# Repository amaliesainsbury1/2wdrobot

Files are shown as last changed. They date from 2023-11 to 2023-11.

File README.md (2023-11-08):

# Abrantix Ax2WDRobot

Assembled Ax2WDRobot

## Overview
The Ax2WDRobot is a 2 Wheel-Drive platform based on espressif's ESP32 module. It is WIFI controlled and has the following features:
- WIFI controlled over an integrated Web-Browser. Supports any platform. *No* Android/Iphone app required
- OLED 128x64 display
- 2 independently controlled DC motors
- Omnivision camera module
- Ultrasonic distance sensor
- 6-axis gyroscope (no firmware support so far)
- LiIon powered (18650 cell)
- Charging and programming over USB-C connector
- Easy to assemble; No soldering required

## Assembly
[Assembly instructions](Doc/assembly_instructions.md)

## Programming
[Programming instructions](Doc/programming.md)

## Troubleshooting
*My Ax2WDRobot doesn't turn on*
1. The battery protection circuit prevents powering on as long as there was no initial charge from USB port.
    - Insert the battery, then connect a USB cable (either from PC or from a USB charger) to start charging/enabling the battery.

*I can't update the firmware; Error during firmware Upload*
1. Please make sure that the required drivers are installed on the machine. For manual installation, see https://www.silabs.com/developers/usb-to-uart-bridge-vcp-drivers?tab=downloads
2. The *Ax2WDRobot* requires a charged battery and must be turned on to upload the firmware

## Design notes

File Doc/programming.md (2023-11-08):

# Abrantix Ax2WDRobot Programming

## Overview

The Ax2WDRobot is based on espressif's ESP32. The provided firmware uses arduino-esp32 toolchain for unified Arduino-Style programming.
For firmware development, Visual Studio Code in conjunction with platformio extension are the recommended tools.

## IDE Installation

1. Navigate to https://code.visualstudio.com/download to download and install Visual Studio Code 
   
2. Start Visual Studio Code and open *Extensions*
   
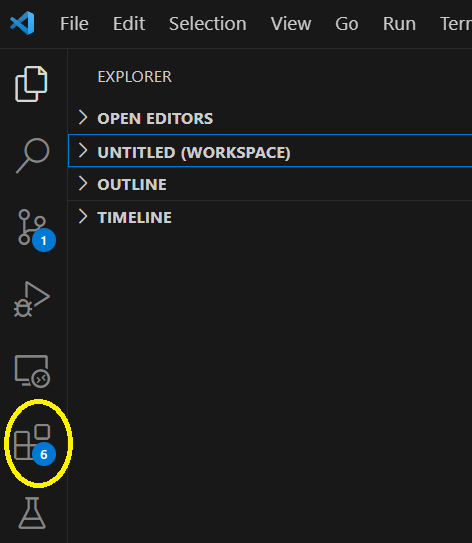
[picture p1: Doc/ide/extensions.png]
Extensions
   

3. In the Extensions screen, search for *platformio* and install it. After installation VS Code has to be restarted.

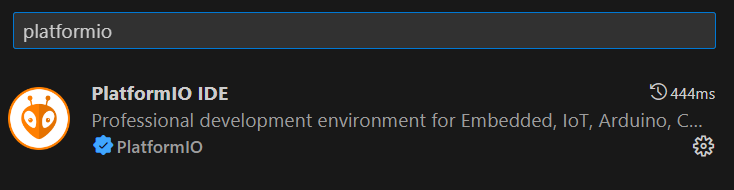
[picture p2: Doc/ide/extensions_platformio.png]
Search Extensions
   

4. Now, you should have a platformio icon in the left toolbar - click on it

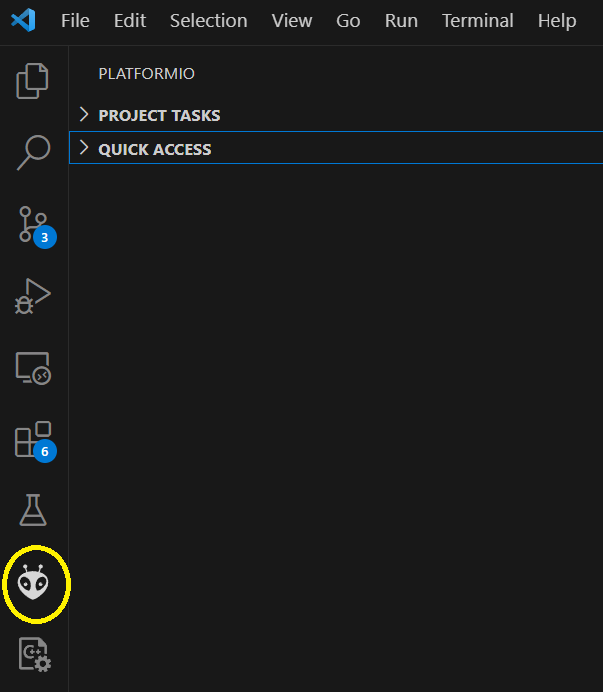
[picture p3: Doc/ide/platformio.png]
Platformio
   

5. In the platformio Home menu, click on *Open project*

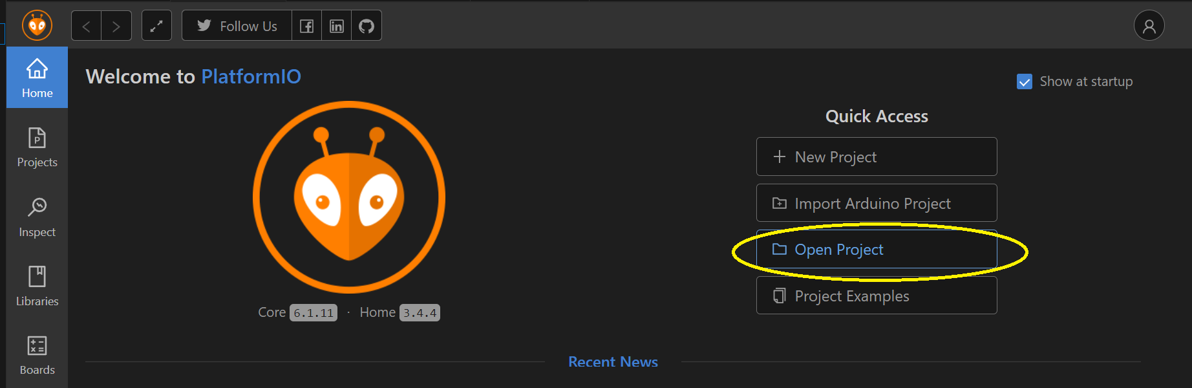
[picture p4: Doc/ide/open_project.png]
Open Project
   

6. Navigate to the folder where you cloned the github project from and open *Ax2WDRobot/firmware/Ax2WDRobot* and click *Open Firmware*.
 
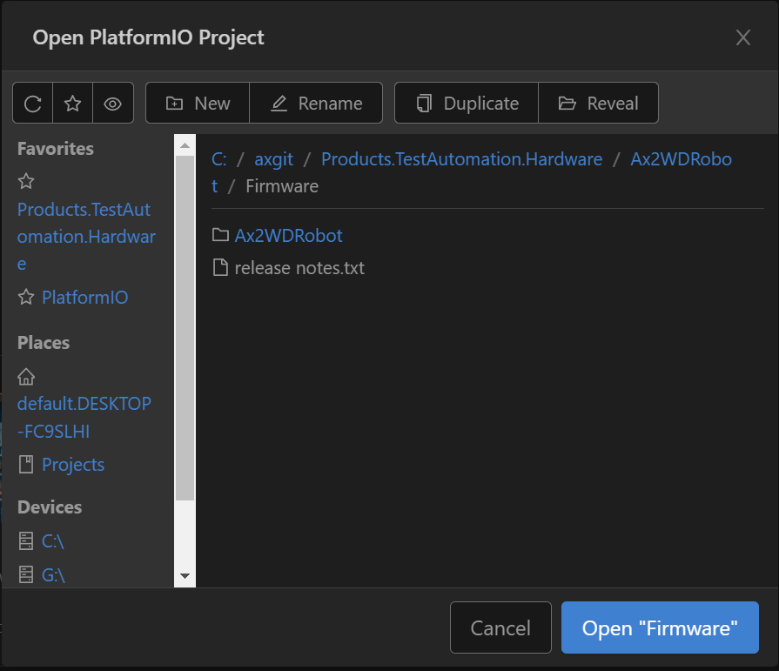
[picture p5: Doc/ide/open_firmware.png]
Open Firmware
   

### Driver installation
The *Ax2WDRobot* uses a Silicon Labs CP210X USB to UART Bridge for communication between PC and robot. Depending on given OS, this driver is already built-in, could be provided as optional Update package or has to be manually installed. In case of a manual installation, please refer to https://www.silabs.com/developers/usb-to-uart-bridge-vcp-drivers?tab=downloads

## Build and upload the firmware
After opening the platformio project, the status bar got some additional icons.
To build, just press the *Check* icon
Build

To upload, first connect the *Ax2WDRobot* to the PC and turn it on. Then, press the *right arrow* icon to build and upload the firmware.
Build

## Build and upload the Filesystem Image
The firmware serves html files from an internal filesystem image which has to be initially loaded, too. This process has to be repeated in case of any change on given files in *data* folder.

1. Click on the platformio icon on the left toolbar
2. Under Project Tasks in the left window, expand *ax2wdrobot->Platform*
3. Execute *Build Filesystem Image*
4. If not already done, connect the *Ax2WDRobot* to the PC and turn it on.
5. Execute *Upload Filesystem Image*

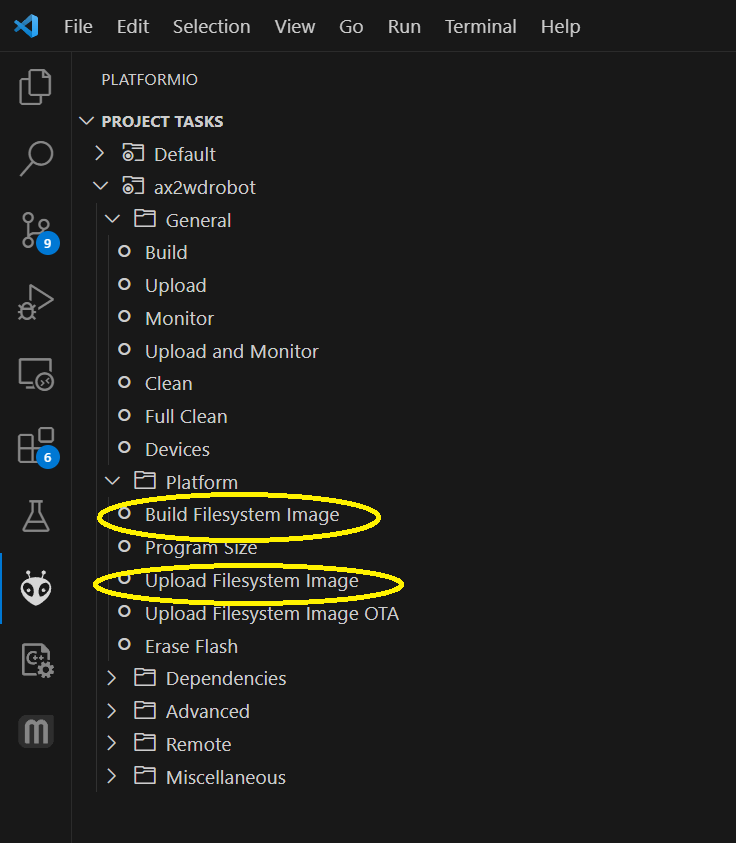
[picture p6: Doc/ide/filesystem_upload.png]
Filesystem upload


For step 4, please ensure that no serial monitor windows are active - otherwise, the filesystem image upload will fail.

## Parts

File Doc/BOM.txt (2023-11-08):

1x Ax2WDRobot Mainboard
1x 18650 Battery i.e. NCR18650B
1x OLED Display 0.96" SSD1306
1x Ultrasonic Sensor RCW-0001
1x Camera-Module OV2640 wide angle 120°
2x TT Gear motor Dual Shaft with Wheel and Dupont wires soldered on
1x Swivel caster roller ~45x28x14mm
1x Zip tie
4x M3 Button Head screw 10mm
2x M3 Button Head screw 14mm
4x M3 Button Head screw 25mm
10x M3 Nut
10x M3 Spring washer
1x roller spacer (3d printed)
2x motor holder (3d printed)

Optional:
1x USB Type A to C data/charging cable

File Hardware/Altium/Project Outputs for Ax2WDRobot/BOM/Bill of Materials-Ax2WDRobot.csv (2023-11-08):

Comment | Description | Designator | Footprint | LibRef | Quantity | LCSCPartNo | Case/Package
1042P | BATTERY HOLDER 18650 SMD TAB | BT1 | FP-1042P-MFG | CMP-19636-000019-1 | 1 | C2988620
22uF/6.3V | Capacitor | C1, C2, C4, C44, C45 | 1608[0603] | Cap | 5 | C59461 | 0603
100nF/50V | Cap Ceramic 0.1uF 50V X7R 20% SMD 0603 125C Paper T/R | C3, C5, C6, C7, C9, C10, C12, C13, C15, C16, C18, C19, C25, C26, C28, C29, C30, C31, C32, C33, C36, C37, C42, C43, C48 | 1608[0603] | C | 25 | C14663 | 0603
15pF/50V | Cap Ceramic 0603 | C8 | 1608[0603] | C | 1 | C1644 | 0603
1uF | CAP CER 1UF 10V X5R 0603 | C11, C14, C17, C20, C22, C23, C34, C38, C40, C41 | 1608[0603] | C | 10 | C15849 | 0603
10uF/10V | Capacitor | C21, C24, C27, C35, C39 | 1608[0603] | C, Cap | 5 | C19702 | 0603
1206 100uF/6.3V | Cap Ceramic 100uF 6.3V X5R ±20% SMD 1206 +85°C Embossed T/R | C49 | FP-CL31-IPC_B | CMP-13271-000821-1 | 1 | C15008
SS34 | 0.5mA@40V 40V Single 3A 0.55V@3A SMA(DO-214AC) Schottky | D1 | DIOM449X264X300L114X135N | EGF1B | 1 | C8678 | SMA
LED-Blue | LED BLUE CLEAR CHIP SMD | D2 | FP-LTST-C193TBKT-5A-MFG | CMP-2000-06624-2 | 1 | C72041 | 0603
LED-Green | LED GREEN CLEAR CHIP SMD | D3 | LED0603G | LED-G | 1 | C72043 | 0603
LED-Red | LED RED CLEAR CHIP SMD | D4 | FP-LTST-C193KRKT-5A-MFG | CMP-2000-06623-2 | 1 | C2286 | 0603
SRV05-4.TCT | RailClamp(R) Low Capacitance TVS Diode Array, 5 pF, 17.5 VC, -55 to 125 degC, 6-Pin SOT23, RoHS, Tape and Reel | D5 | SMTC-SOT23-6_V | CMP-2000-05358-1 | 1 | C85364 | SOT-23-6L
PTC 6V 750mA | PTC RESET FUSE 6V 750MA 1206 | F1 | FP-1206L050YR-MFG | CMP-08606-000073-1 | 1 | C70078 | 1206
22uH/2A | Inductor | L1 | INDM7166X18N | Inductor | 1 | C705336
500mA 1.5K@100MHz | Chip Ferrite Bead, 0603, 1500O @ 100MHz, 0.5O, 25%, 500mA | L2, L3, L4, L5, L6 | 1608[0603] | CMP-0686-00368-3 | 5 | C82155 | 0603
Header 4 female 8.5mm | Header, 4-Pin | P1, P4 | BCS-104-L-S-TE | Header 4 | 2 | C124413
FPC Connector 24 pins, top connect |  | P2 | AFC07-S24ECA-00 | FPC-CONN-24 | 1 | C262643
TYPE-C-31-M-12 | USB Connectors 24 Receptacle 1 8.94*7.3mm RoHS | P3 | HRO_TYPE-C-31-M-12-3D | TYPE-C-31-M-12 | 1 | C165948
Header 2 | Header, 2-Pin | P5, P6 | BCS-102-L-S-TE | Header 2 | 2 | C49661
FS8205 | Dual N-Channel Enhancement Mode Power MOSFET | Q1, Q5 | SOT95P280X145-6N | FS8205 | 2 | C2830320
MMSS8050 | TRANS NPN 25V 1.5A SOT23 | Q2, Q3 | SOT-23 | NPN1 | 2 | C20526 | SOT-23
AO3401A | P-Channel MOSFET, 30 V, 4 A, -55 to 150 degC, 3-Pin SOT-23-3L, RoHS, Tape and Reel | Q4, Q6 | AO-SOT-23-3L_V | CMP-2000-05778-1 | 2 | C15127
27K | Resistor | R1 | J1-0603 | Res3 | 1 | C22967
2K4 | Res General Purpose Thick Film 0603 1% 1/10W ±100ppm/°C Molded SMD Paper T/R | R2 | 1608[0603] | R | 1 | C22940 | 0603
2K7 | Resistor | R3 | J1-0603 | Res3 | 1 | C13167
1k | Res General Purpose Thick Film 0603 1% 1/10W ±100ppm/°C Molded SMD Paper T/R | R4, R6, R9, R14, R27 | 1608[0603] | R | 5 | C21190 | 0603
11K | Resistor | R5 | J1-0603 | Res3 | 1 | C25950 | 0603
1K2 | Resistor | R7 | J1-0603 | Res3 | 1
100R | Resistor | R8 | J1-0603 | Res3 | 1
4k7 | RES SMD 4.7K OHM 1% 1/10W 0603, Res General Purpose Thick Film 0603 1% 1/10W ±100ppm/°C Molded SMD Paper T/R | R10, R11, R15, R16, R20, R25, R26, R31, R32, R33 | 1608[0603] | R | 10 | C23162 | 0603
470R | YAGEO RC0603FR-07470RL SMD Chip Resistor, Thick Film, 470 ohm, 50 V, 0603 [1608 Metric], 100 mW, 1%, RC Series | R17 | 1608[0603] | R | 1 | C23179 | 0603
12k | Res Thick Film 0603 12K Ohm 1% 1/10W 100ppm/C Molded SMD SMD Paper T/R | R18, R19, R21, R22 | 1608[0603] | R | 4 | C22790 | 0603
5k1 | Res Thick Film 0603 5.1KOhm 1% 1/10W 100ppm/C Molded SMD SMD Paper T/R | R23, R24 | 1608[0603] | R | 2 | C23186 | 0603
510R | Res General Purpose Thick Film 0603 1% 1/10W ±100ppm/°C Molded SMD Paper T/R | R28 | 1608[0603] | R | 1 | C23193 | 0603
0R | Res General Purpose Thick Film 0603 1% 1/10W ±100ppm/°C Molded SMD Paper T/R | R29 | 1608[0603] | R | 1 | C21189 | 0603
620R | Res General Purpose Thick Film 0603 1% 1/10W ±100ppm/°C Molded SMD Paper T/R | R30 | 1608[0603] | R | 1 | C23220 | 0603
PCM12SMTR | SWITCH SLIDE SPDT 300MA 6V | SW1 | FP-PCM12SMTR-MFG | CMP-2000-06884-2 | 1 | C109335
B3F-4055 | Tactile Switch, 1 to 50 mA, 100 mOhm Max, 5 to 24 VDC, -25 to 70 degC, 4-Pin THD, RoHS, Bulk | SW2 | OMRON-B3F-4055_AX | CMP-2000-05902-1 | 1 | C84931
MT3608 | High Efficiency 1.2MHz 2A Step Up Converter | U1 | SOT95P280X145-6N | MT3608 | 1 | C84817
TP4056 | Complete single cell Li-Ion battery with a constant current / constant voltage linear charger | U2 | SOP127P600X175-9N | TP4056 | 1 | C16581
TC7SB3157 | 1-of-2 multiplexer/demultiplexer | U3 | SOT-363_MP6D | TC7SB3157CFU | 1 | C2674458
TC118S |  | U4, U5 | SO08 | TC118S | 2 | C88308
CP2102N | Full Speed USB to UART Bridge USB 2.0 3.3V Tube Automotive 28-Pin QFN EP | U6 | QFN28_5X5_SIL | CP2102N-A02-GQFN28 | 1 | C6568 | QFN28
ESP32-WROVER-E | Bluetooth, WiFi 802.11b/g/n, Bluetooth v4.2 + EDR, Class 1, 2 and 3 Transceiver Module 2.4GHz ~ 2.5GHz PCB Trace Surface Mount | U7 | XCVR_ESP32-WROVER | ESP32-WROVER | 1 | C2973667
LM317MDT-TR | 500mA, Medium Current 1.2 to 37 V Adjustable Voltage Regulator, 3-Pin DPAK, Tape and Reel | U8, U9 | TO-252_M | CMP-0244-00074-1 | 2 | C75510 | DPAK
AZ1117EH-3.3V | IC REG LIN 3.3V 800MA SOT223-4 | U10 | SOT-223 | AZ1117EH-3.3V | 1 | C6186 | SOT-223
DW01A | SOT-23-6L Battery Management ICs ROHS | U11 | SOT23-6 | DW01A | 1 | C351410
LIS2DW12TR | ACCEL 2-16G I2C/SPI 12LGA | U12 | FP-LGA12-DM00170568-MFG | CMP-12175-000006-1 | 1 | C189624

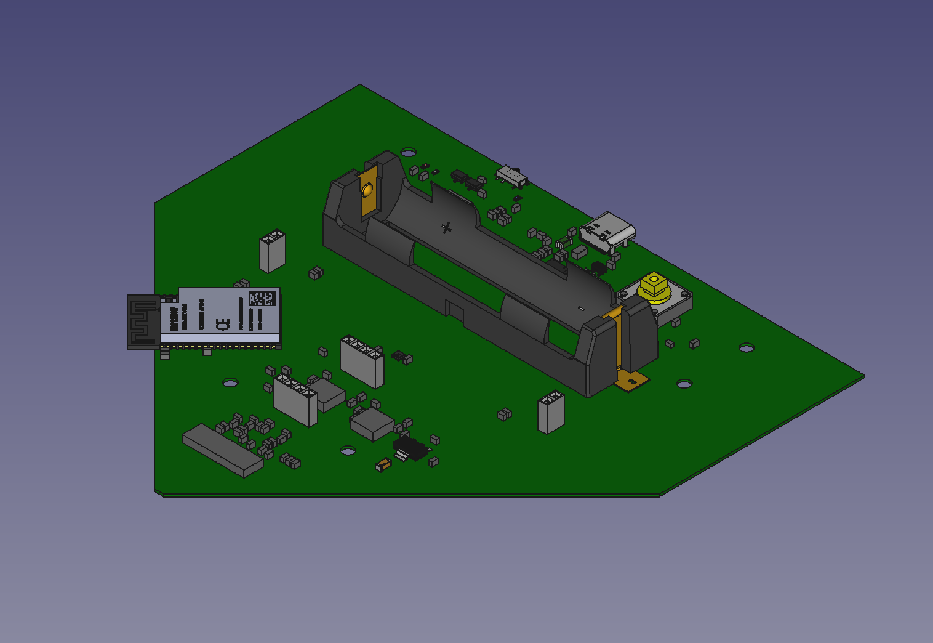
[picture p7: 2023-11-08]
Doc/parts/Mainboard.png

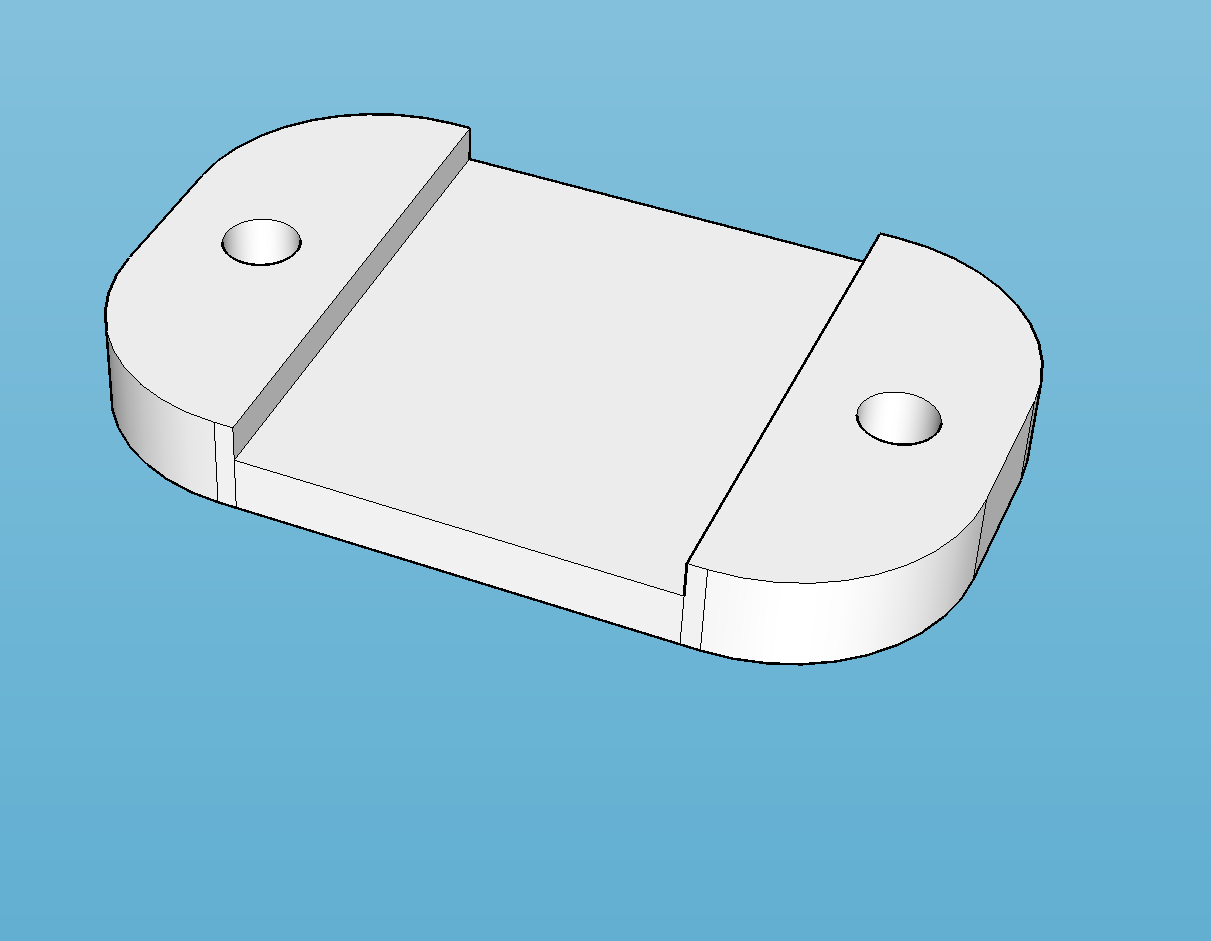
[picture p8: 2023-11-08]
Doc/parts/Roller_spacer.png

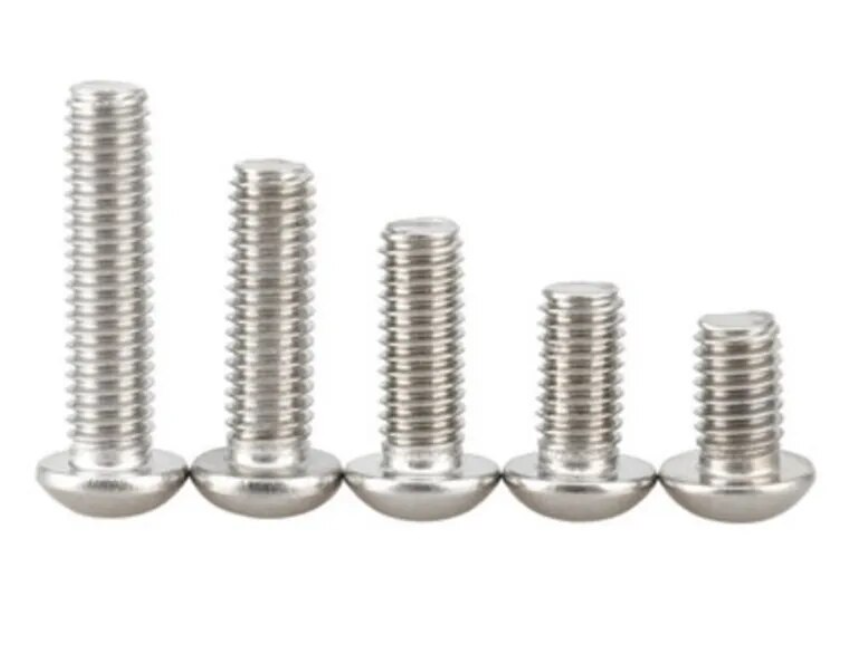
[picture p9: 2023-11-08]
Doc/parts/Screws.png

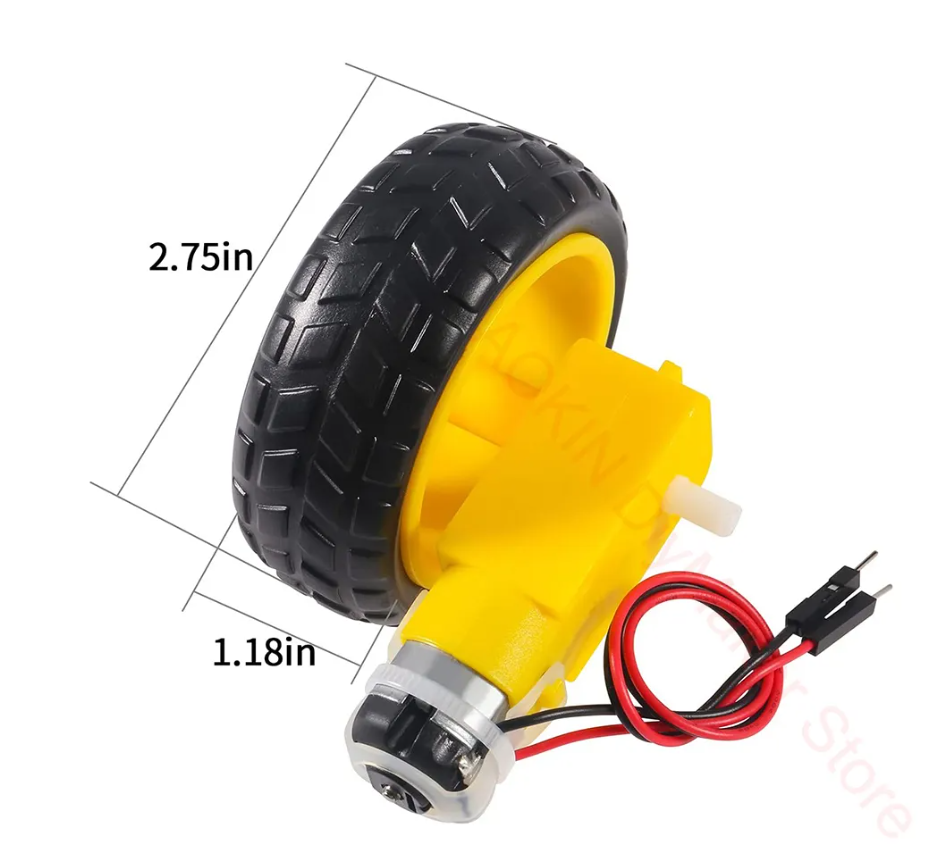
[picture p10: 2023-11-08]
Doc/parts/Motor.png

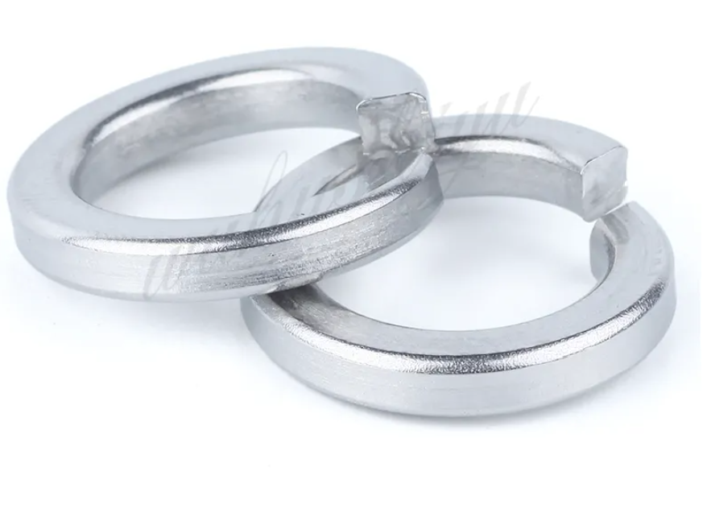
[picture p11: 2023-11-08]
Doc/parts/Washers.png

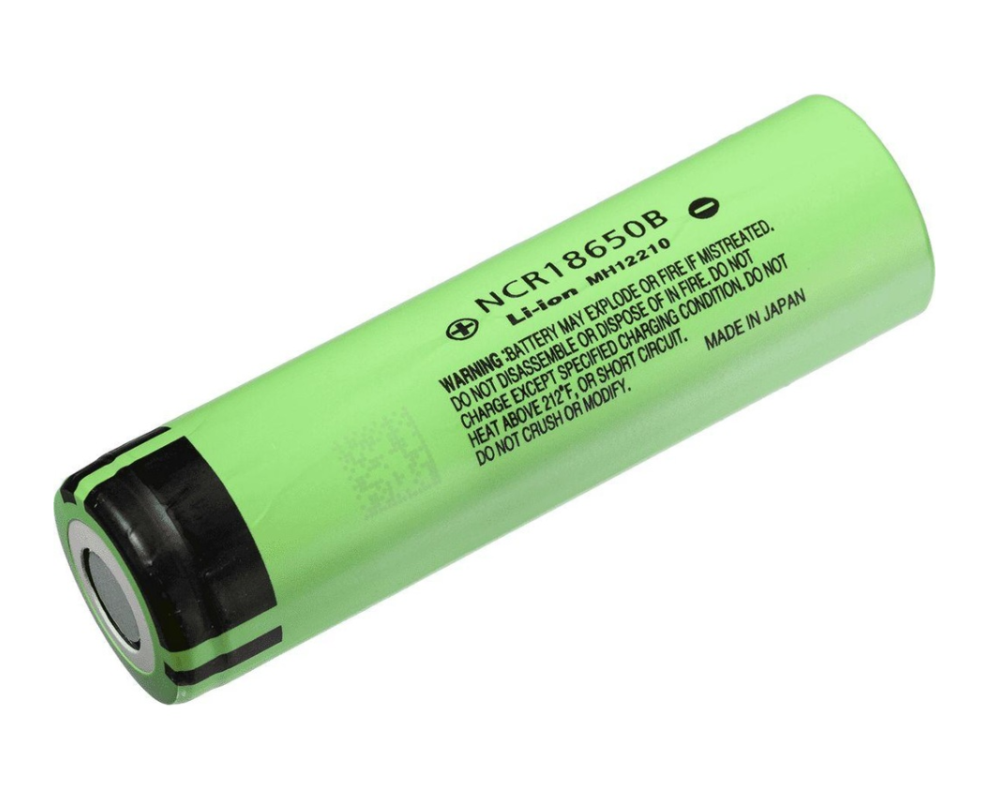
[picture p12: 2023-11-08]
Doc/parts/Battery.png

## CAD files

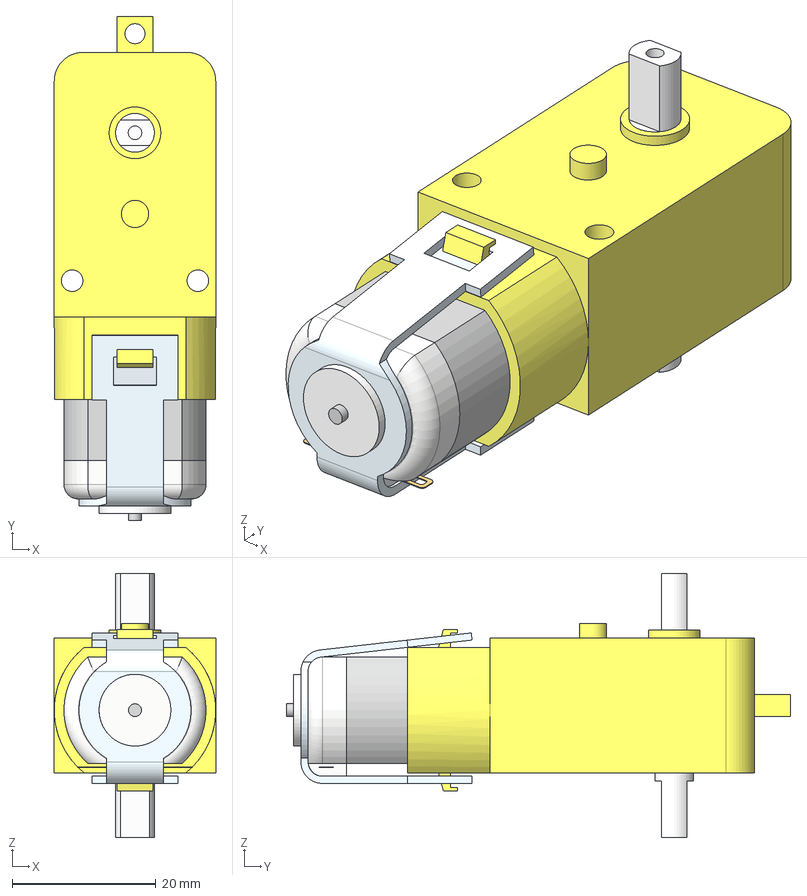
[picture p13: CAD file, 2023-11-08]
Hardware/Altium/TT Motor.step
22.5 x 70.2 x 36.8 mm

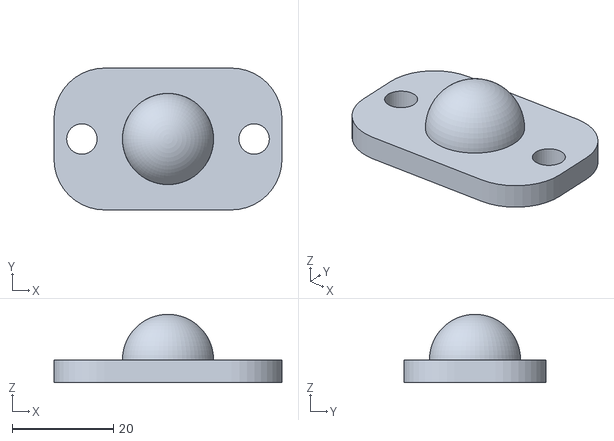
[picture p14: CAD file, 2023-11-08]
Hardware/Housing/roller.stl
45.0 x 28.0 x 13.5

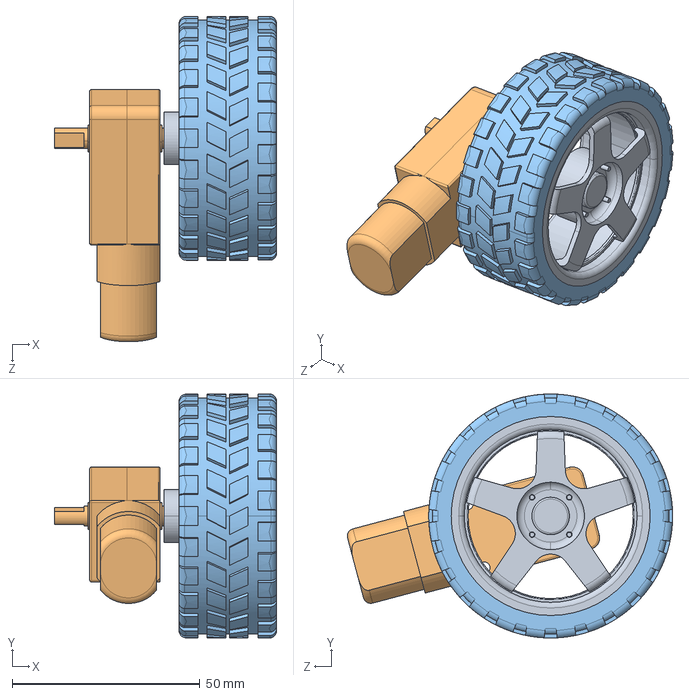
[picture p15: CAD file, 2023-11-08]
Hardware/Altium/dc_motor_and_wheel.STEP
59.2 x 65.0 x 86.7 mm

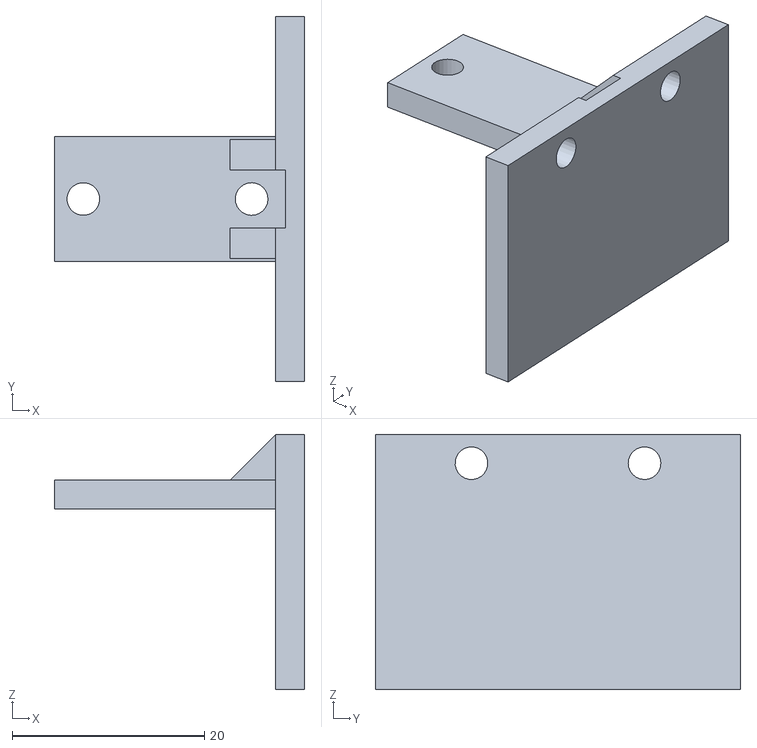
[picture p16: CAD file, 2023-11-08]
Hardware/Housing/motor_holder.stl
26.0 x 38.0 x 26.5

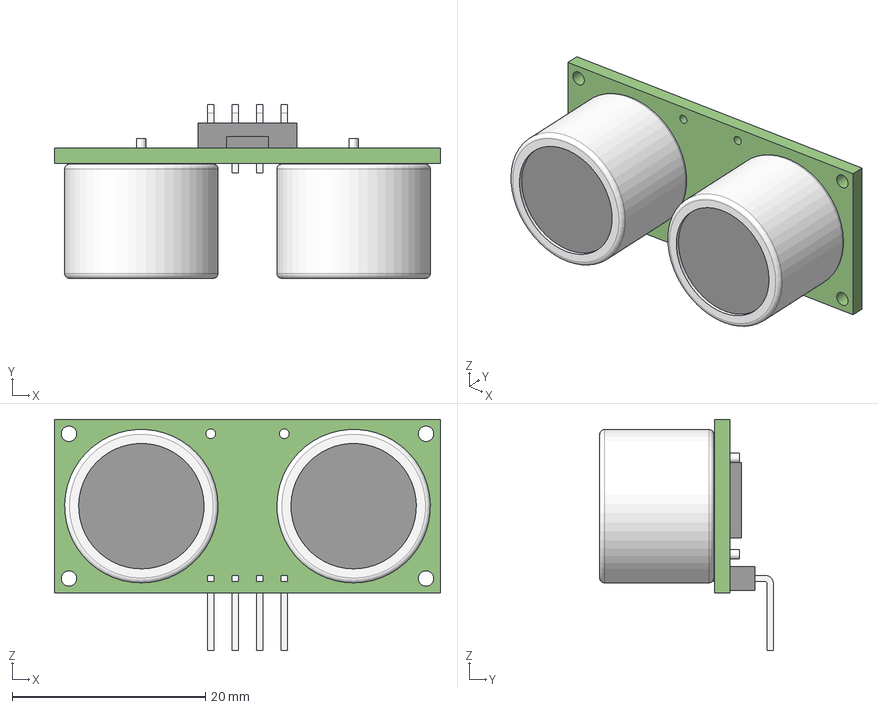
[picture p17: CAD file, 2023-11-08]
Hardware/Altium/RCWL-1601.step
40.0 x 18.0 x 24.0 mm

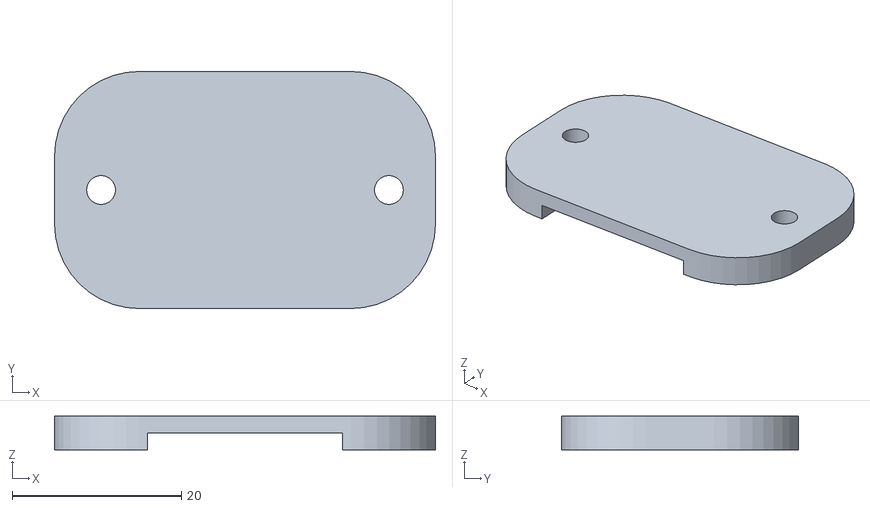
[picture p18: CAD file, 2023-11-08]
Hardware/Housing/roller_spacer.stl
45.0 x 28.0 x 4.00

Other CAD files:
Hardware/Altium/TT_Motor.stl
Hardware/Housing/motor_holder.skp
Hardware/Housing/roller.skp

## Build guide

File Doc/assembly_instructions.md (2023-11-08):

# Abrantix Ax2WDRobot Assembly instructions

## Parts

- 1x Ax2WDRobot Mainboard
- 1x 18650 Battery i.e. NCR18650B
- 1x OLED Display 0.96" SSD1306
- 1x Ultrasonic Sensor RCW-0001
- 1x Camera-Module OV2640 wide angle 120°
- 2x TT Gear motor Dual Shaft with Wheel and Dupont wires soldered on
- 1x Swivel caster roller ~45x28x14mm
- 1x Zip tie
- 4x M3 Button Head screw 10mm
- 2x M3 Button Head screw 14mm
- 4x M3 Button Head screw 25mm
- 10x M3 Nut
- 10x M3 Spring washer
- 1x roller spacer (3d printed)
- 2x motor holder (3d printed)

Optional:
- 1x USB Type A to C data/charging cable

## Assembly Step 1

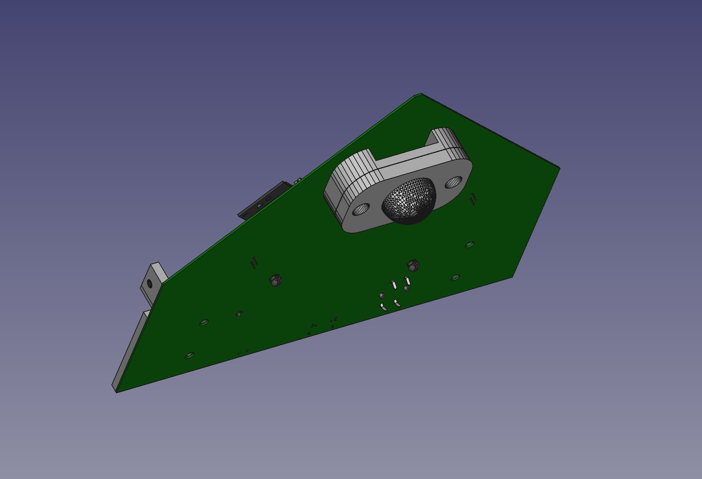
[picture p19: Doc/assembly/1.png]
Step 1


### Required parts
- 1x Ax2WDRobot Mainboard
- 1x Swivel caster roller
- 1x roller spacer (3d printed)
- 2x M3 Button Head screw 14mm
- 2x M3 Nut
- 2x M3 Spring washer

### Instructions
Grab the Ax2WDRobot Mainboard and screw on the swivel caster roller and roller spacer to the bottom of the Mainboard by using two M3x14mm screws

## Assembly Step 2

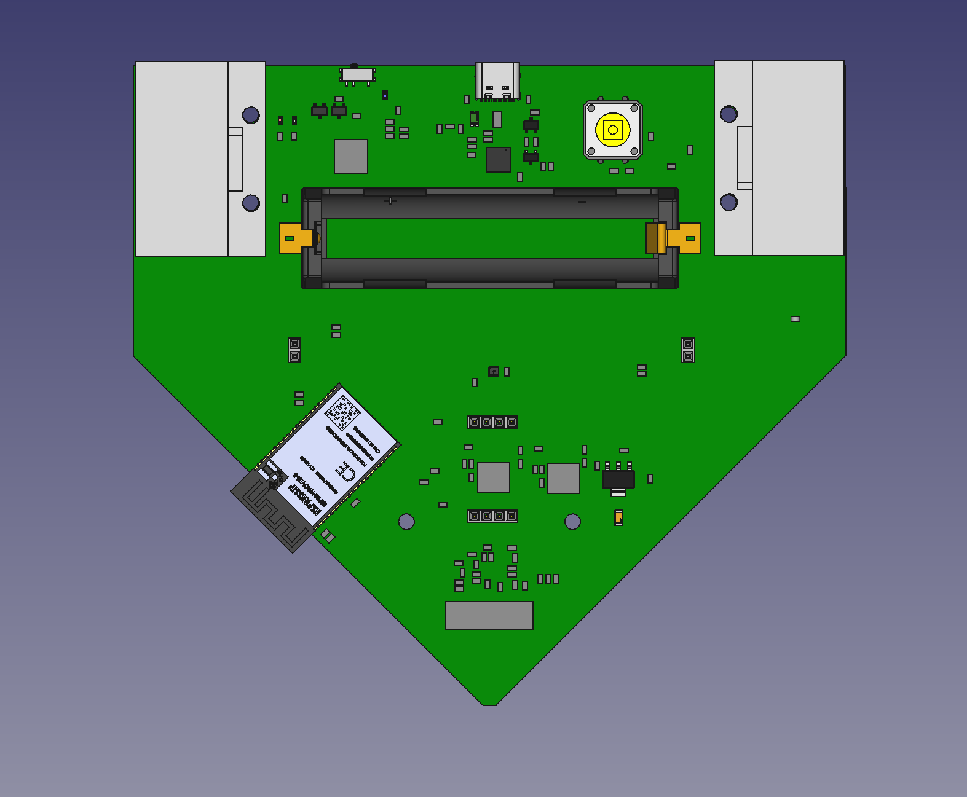
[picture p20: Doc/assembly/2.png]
Step 2


### Required parts
- 2x motor holder (3d printed)
- 4x M3 Button Head screw 10mm
- 4x M3 Nut
- 4x M3 Spring washer

### Instructions
Screw on the two motor holders by using M3x10mm screws

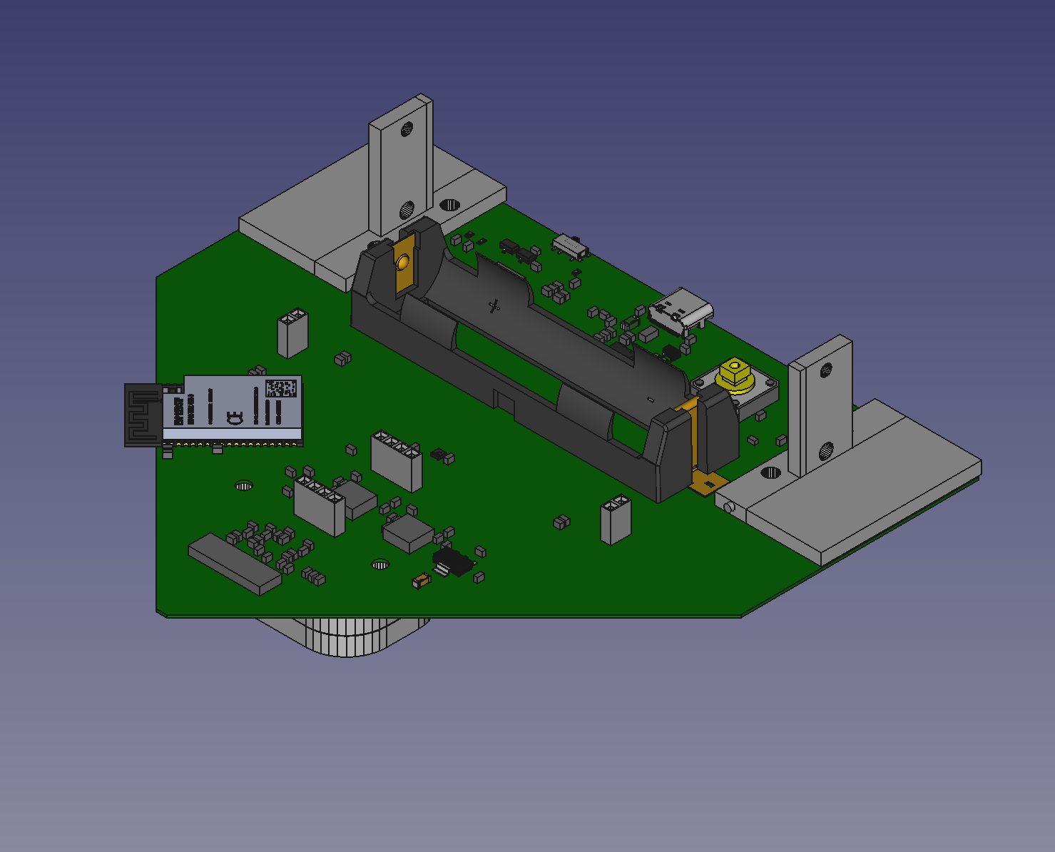
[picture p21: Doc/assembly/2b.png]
Result Step 2


## Assembly Step 3

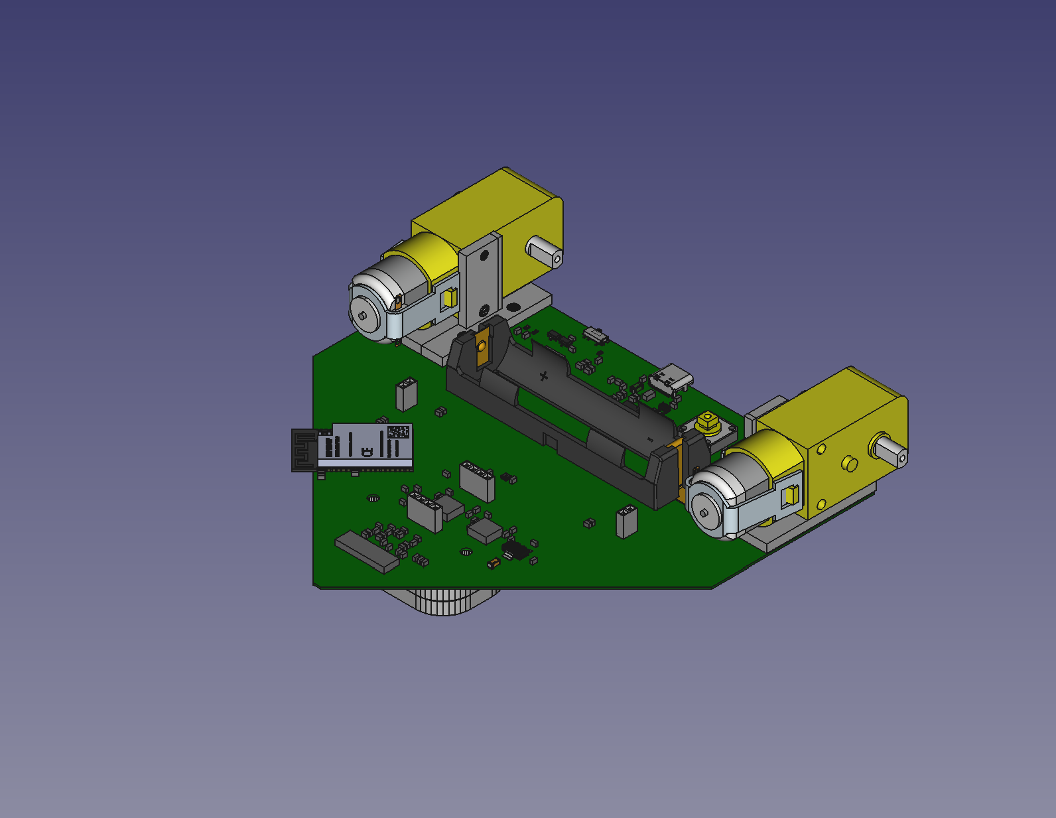
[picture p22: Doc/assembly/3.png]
Step 3


### Required parts
- 2x TT Gear motor assembly
- 4x M3 Button Head screw 25mmm
- 4x M3 Nut
- 4x M3 Spring washer

### Instructions
Screw on the two motors to the holders by using M3x25mm screws

## Assembly Step 4

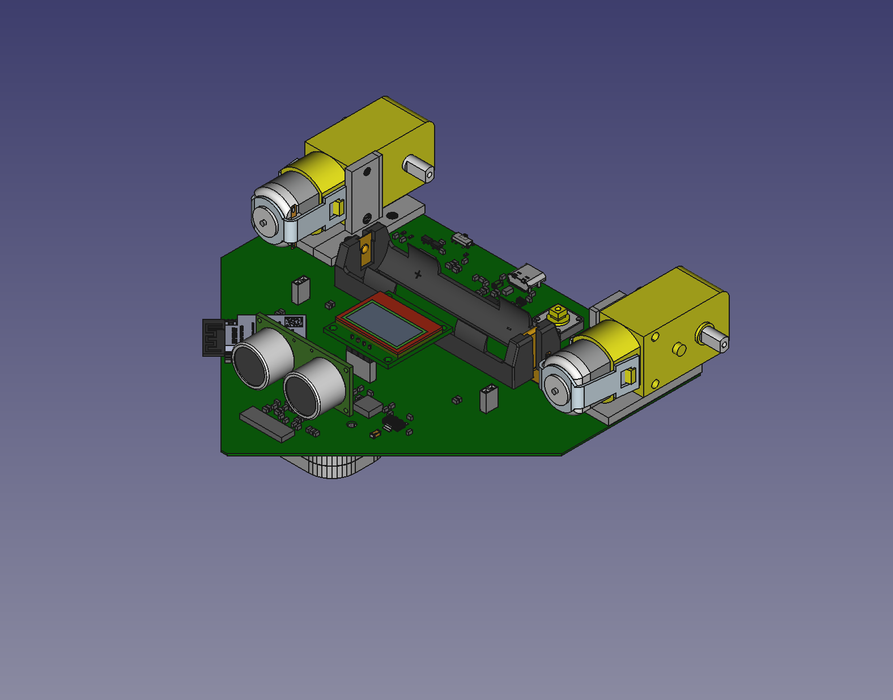
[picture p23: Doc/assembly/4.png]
Step 4


### Required parts
- 1x Camera-Module OV2640 wide angle 120°
- 1x OLED Display 0.96" SSD1306
- 1x Ultrasonic Sensor RCW-0001

### Instructions
Unlock the cam connector by sliding the grey locking clip to the front edge of the mainboard. 
Insert the Camera-Module into the connector by facing its contacts upside
Lock the cam connector by sliding the grey locking clip back
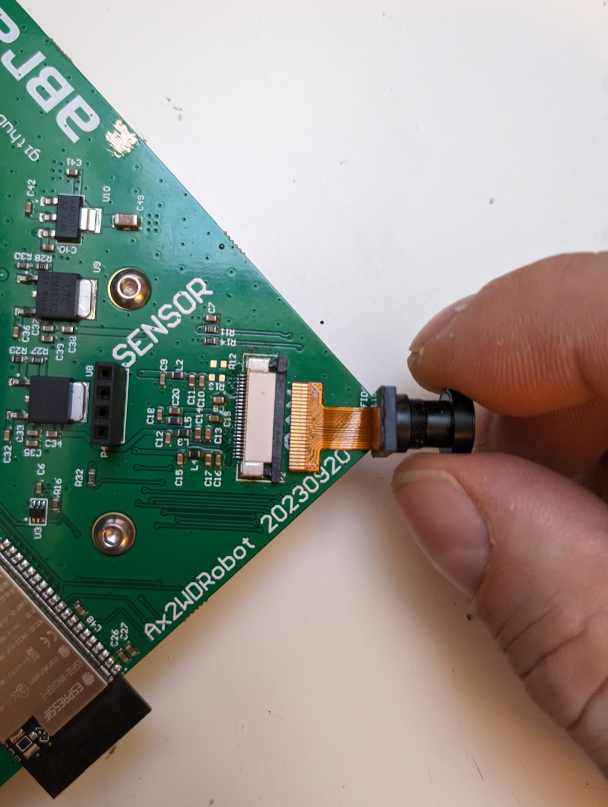
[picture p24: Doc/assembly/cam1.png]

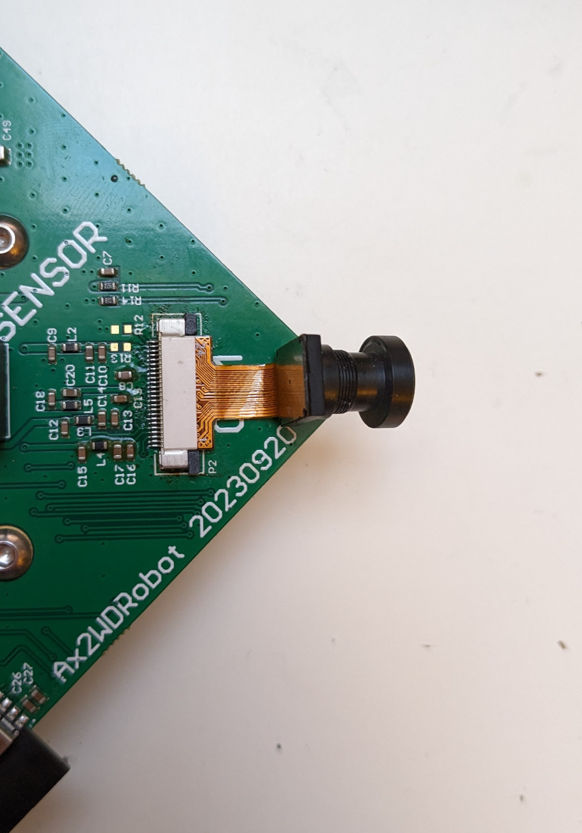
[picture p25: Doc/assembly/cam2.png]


Slightly bend the pins of the Ultrasonic distance sensor by ~30° and insert it into the *SENSOR* connector
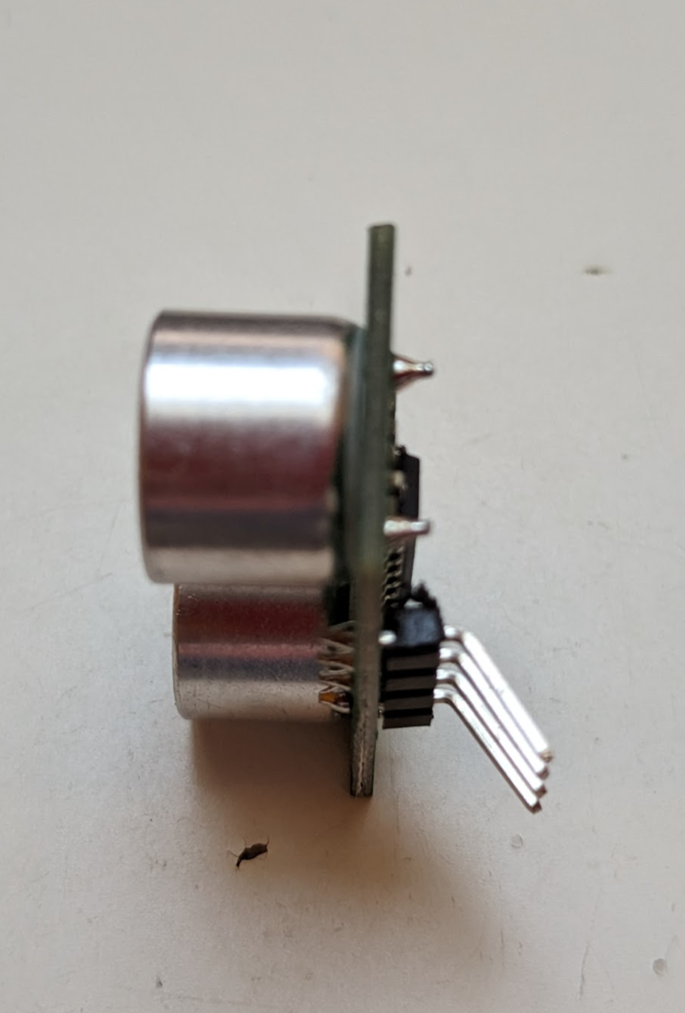
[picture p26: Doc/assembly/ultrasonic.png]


Insert the OLED Display into the *DISPLAY* connector

Plug in the motor connectors (red means *+*, black means *-*). Please connect them "cross-over": the left motor goes to the connector on the right side of the mainboard and vice-versa. Add a zip tie to the cables for better fixation

Finally, insert the 18650 battery into the battery compartment. **IMPORTANT: Check polarity of battery before inserting.**

## Glueing
For better fixation, it's recommended to apply a small amount of (hot) glue to the motor Dupont connectors and the cam.

Final

Now, your Ax2WDRobot is ready to be charged and flashed.

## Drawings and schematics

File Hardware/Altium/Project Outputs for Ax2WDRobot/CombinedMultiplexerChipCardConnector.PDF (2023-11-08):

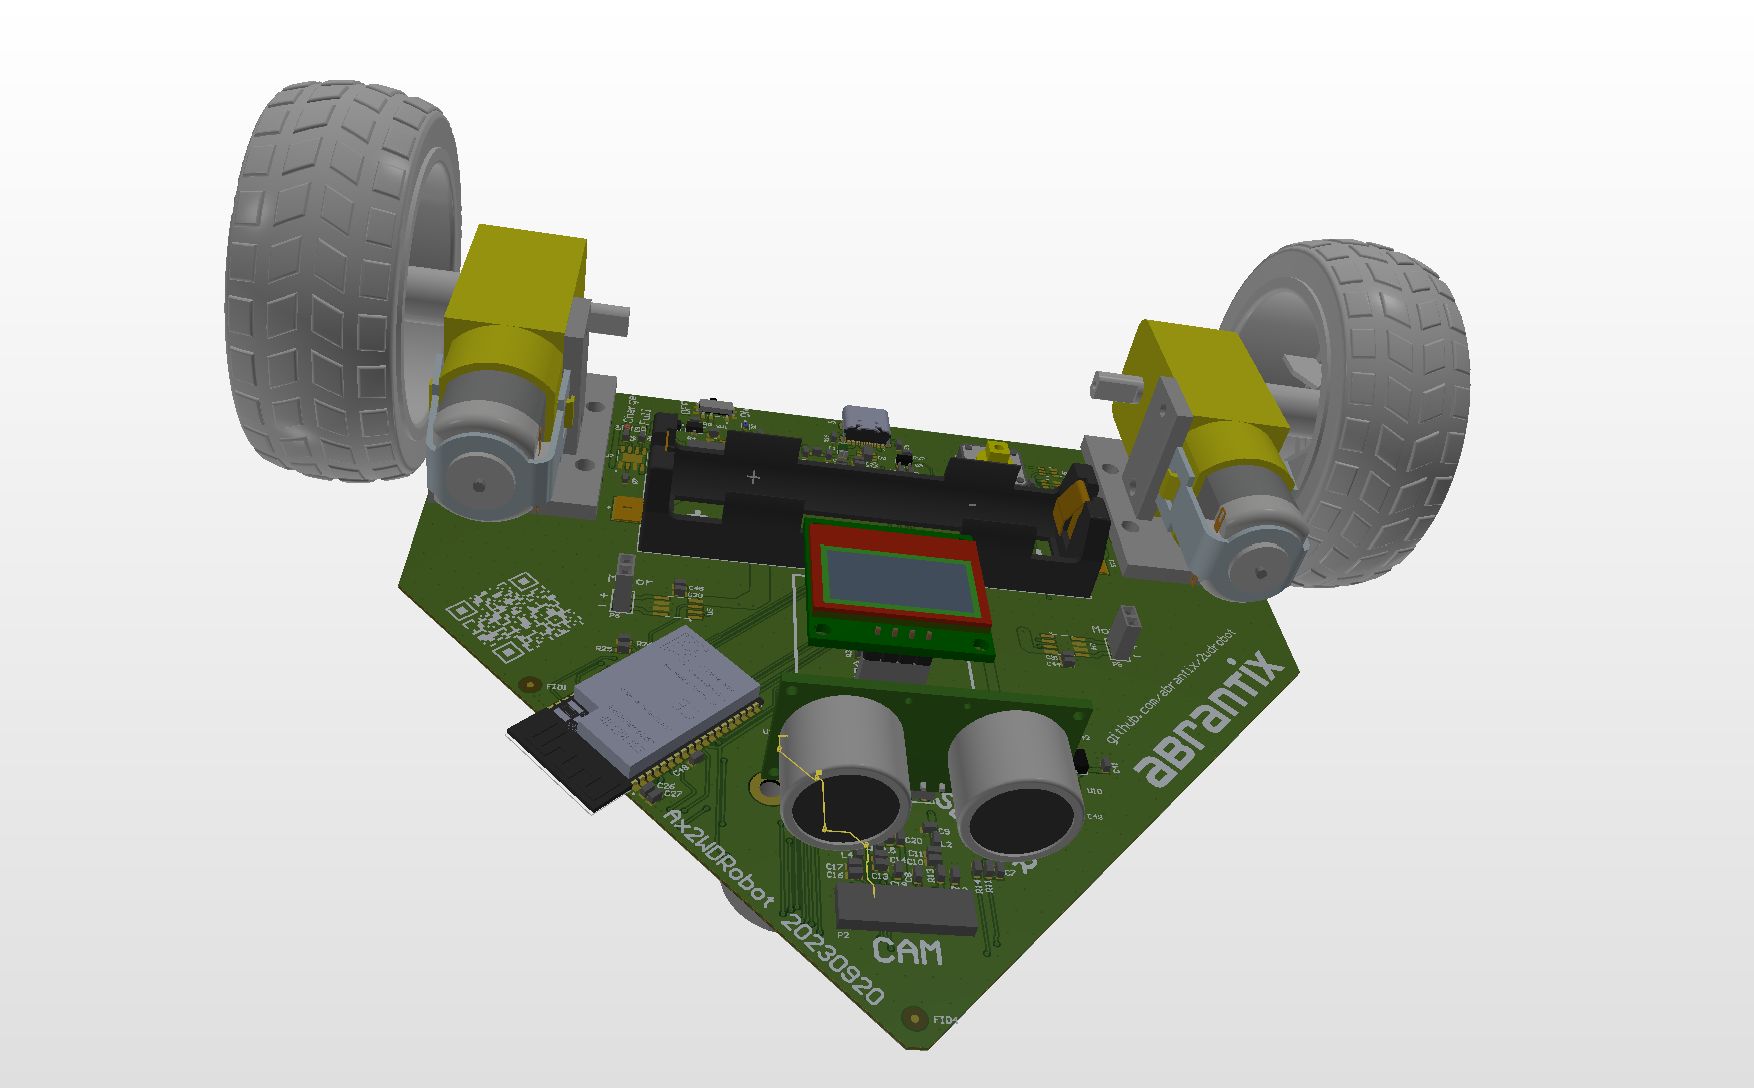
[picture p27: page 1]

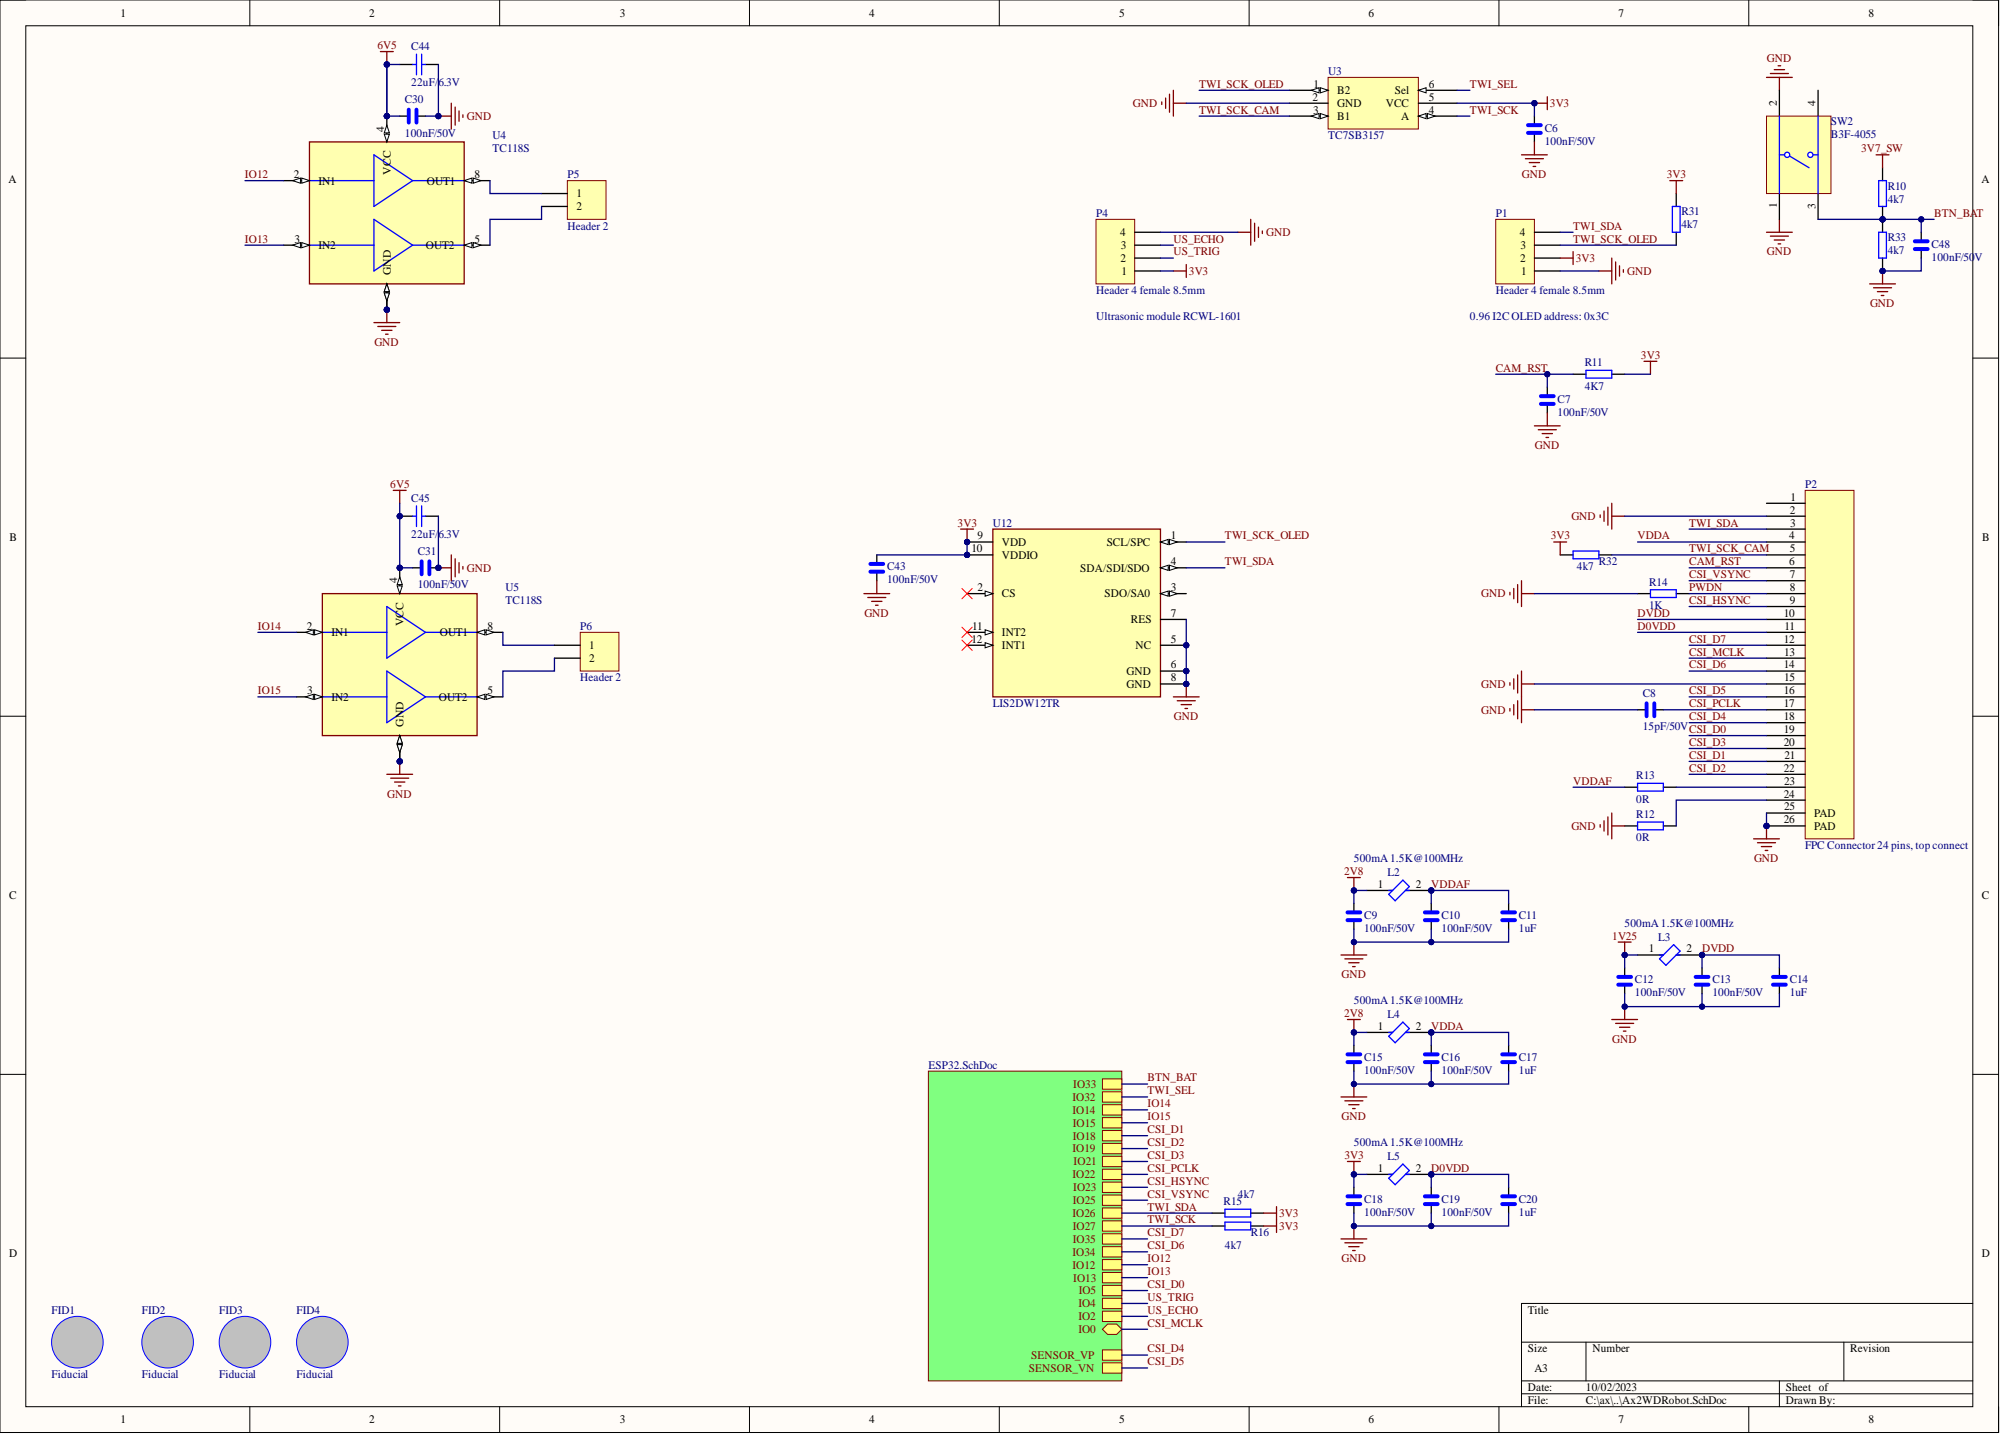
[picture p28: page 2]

FPC Connector 24 pins, top connect

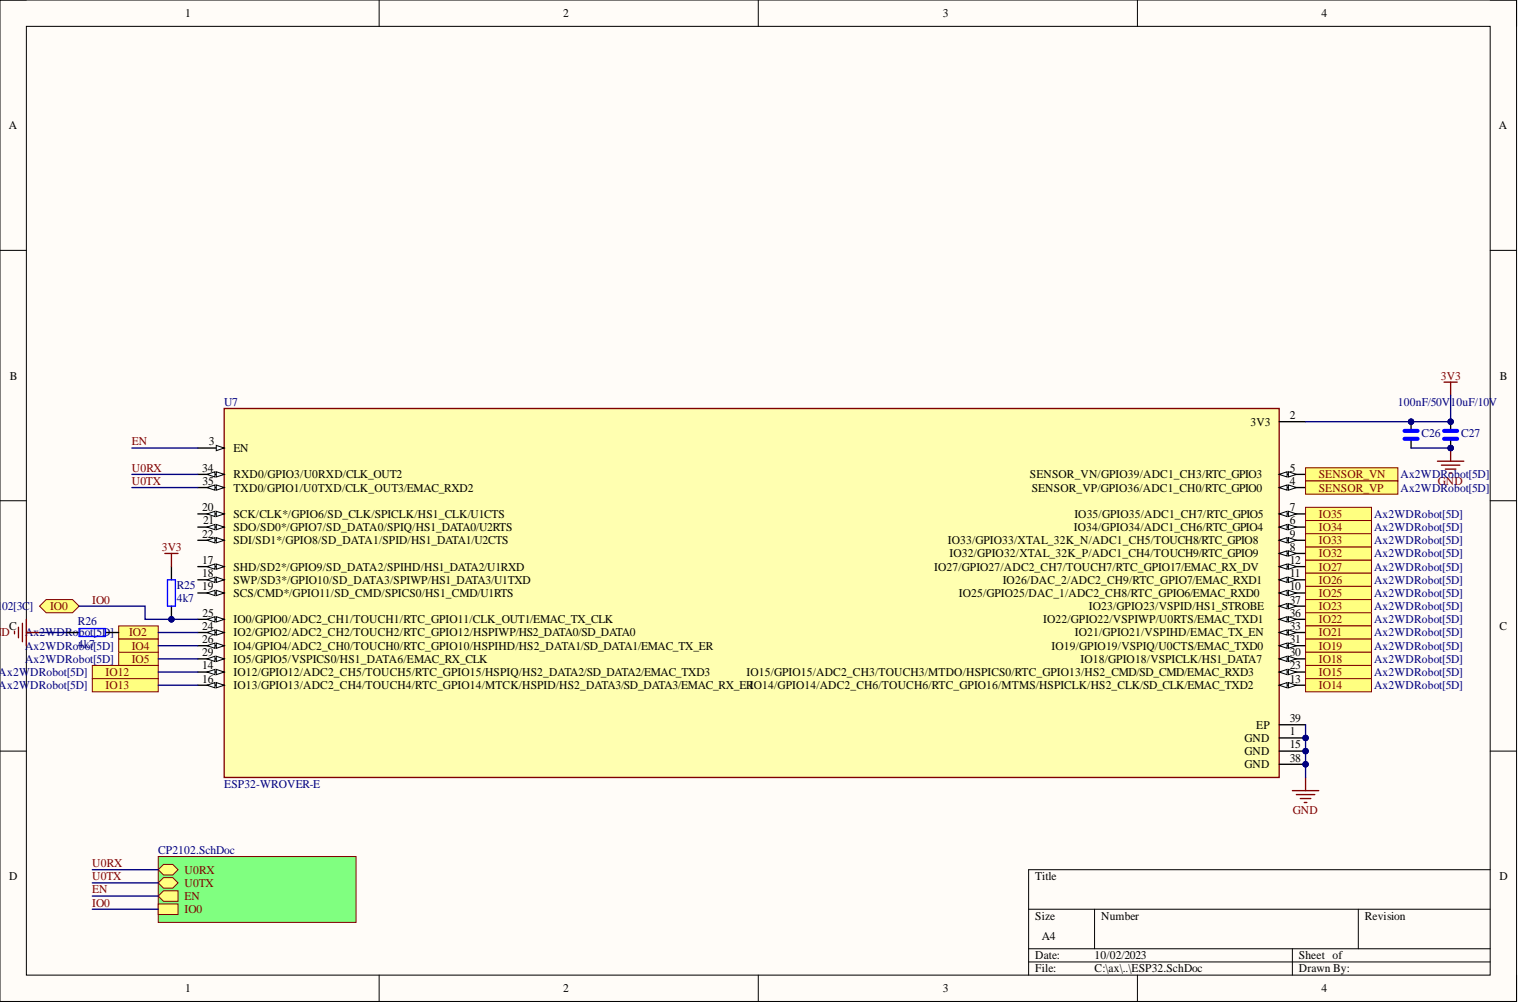
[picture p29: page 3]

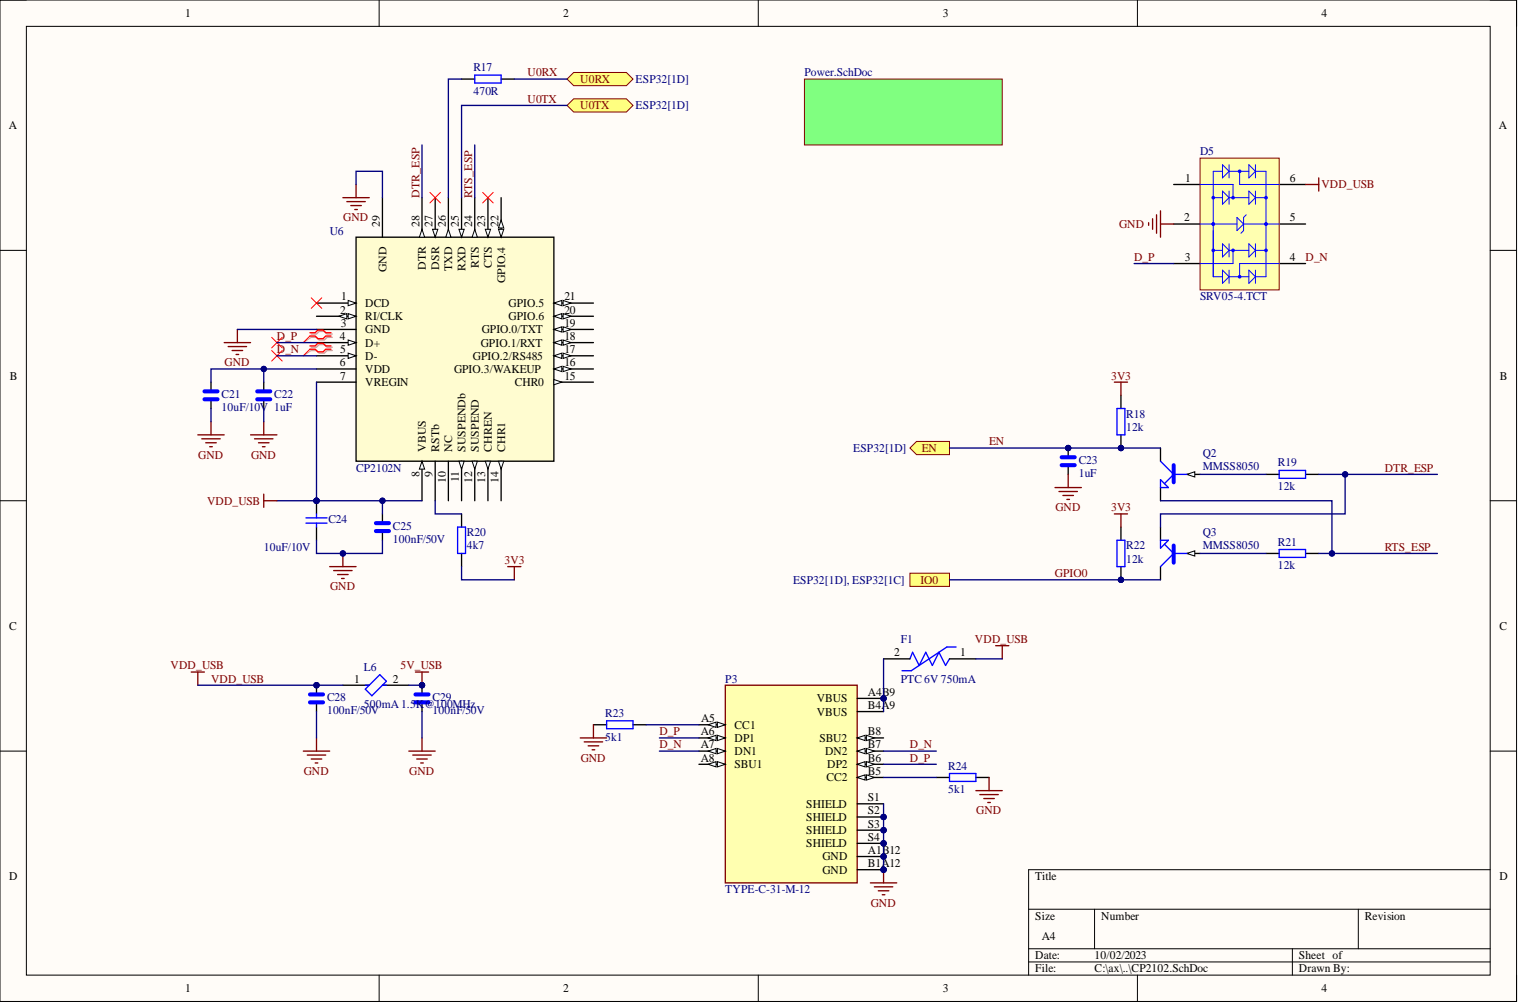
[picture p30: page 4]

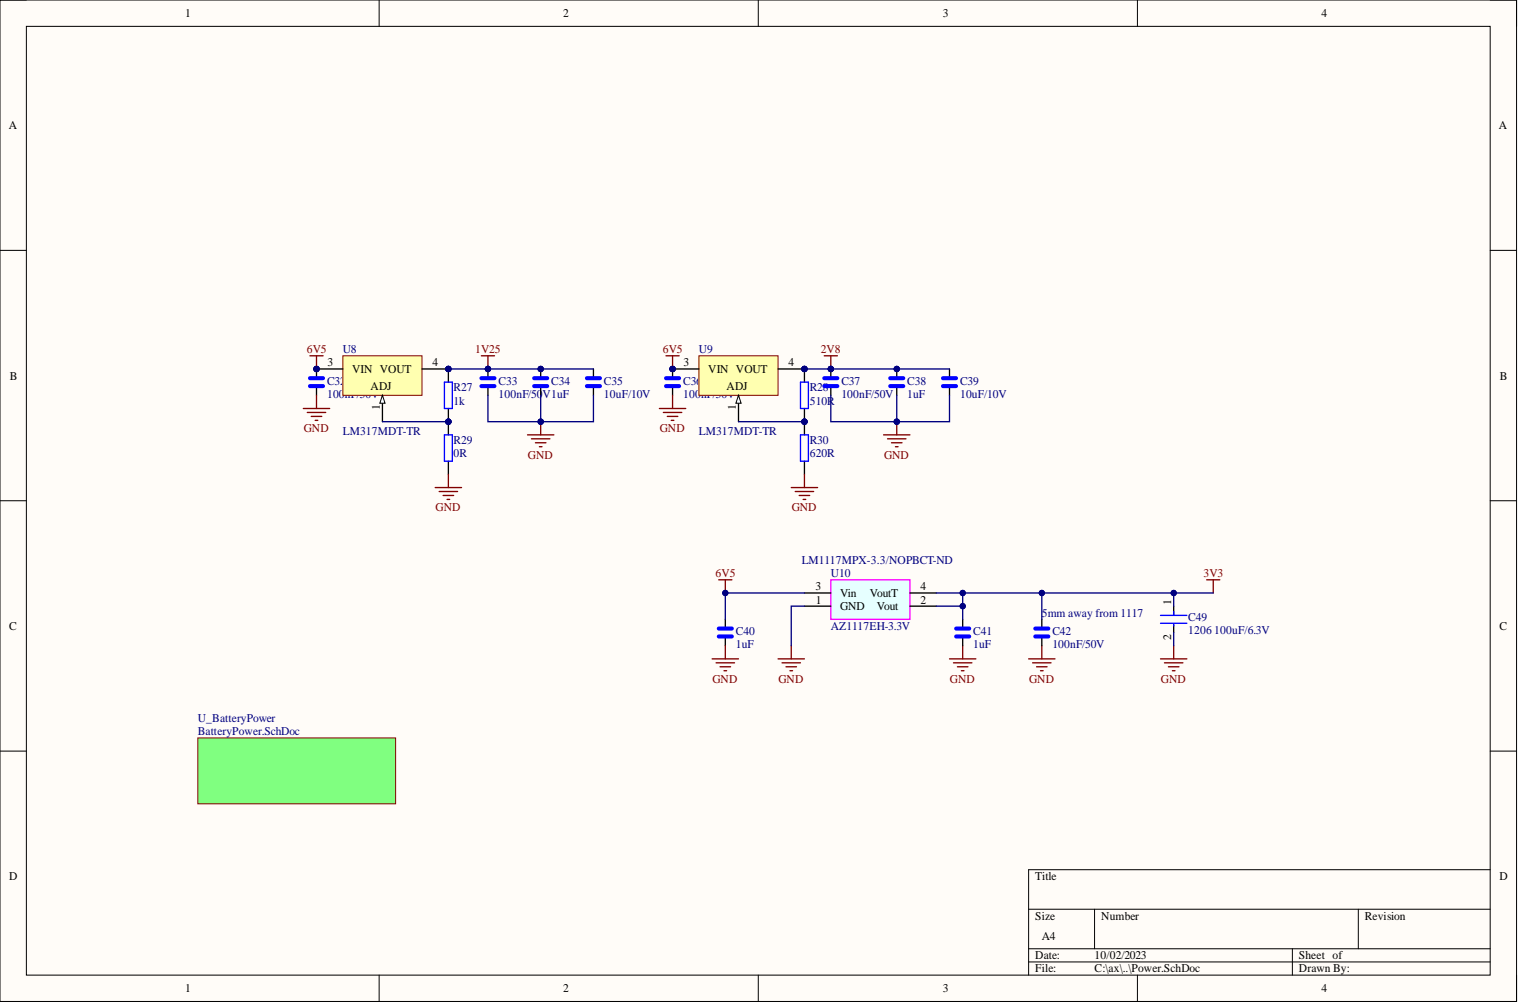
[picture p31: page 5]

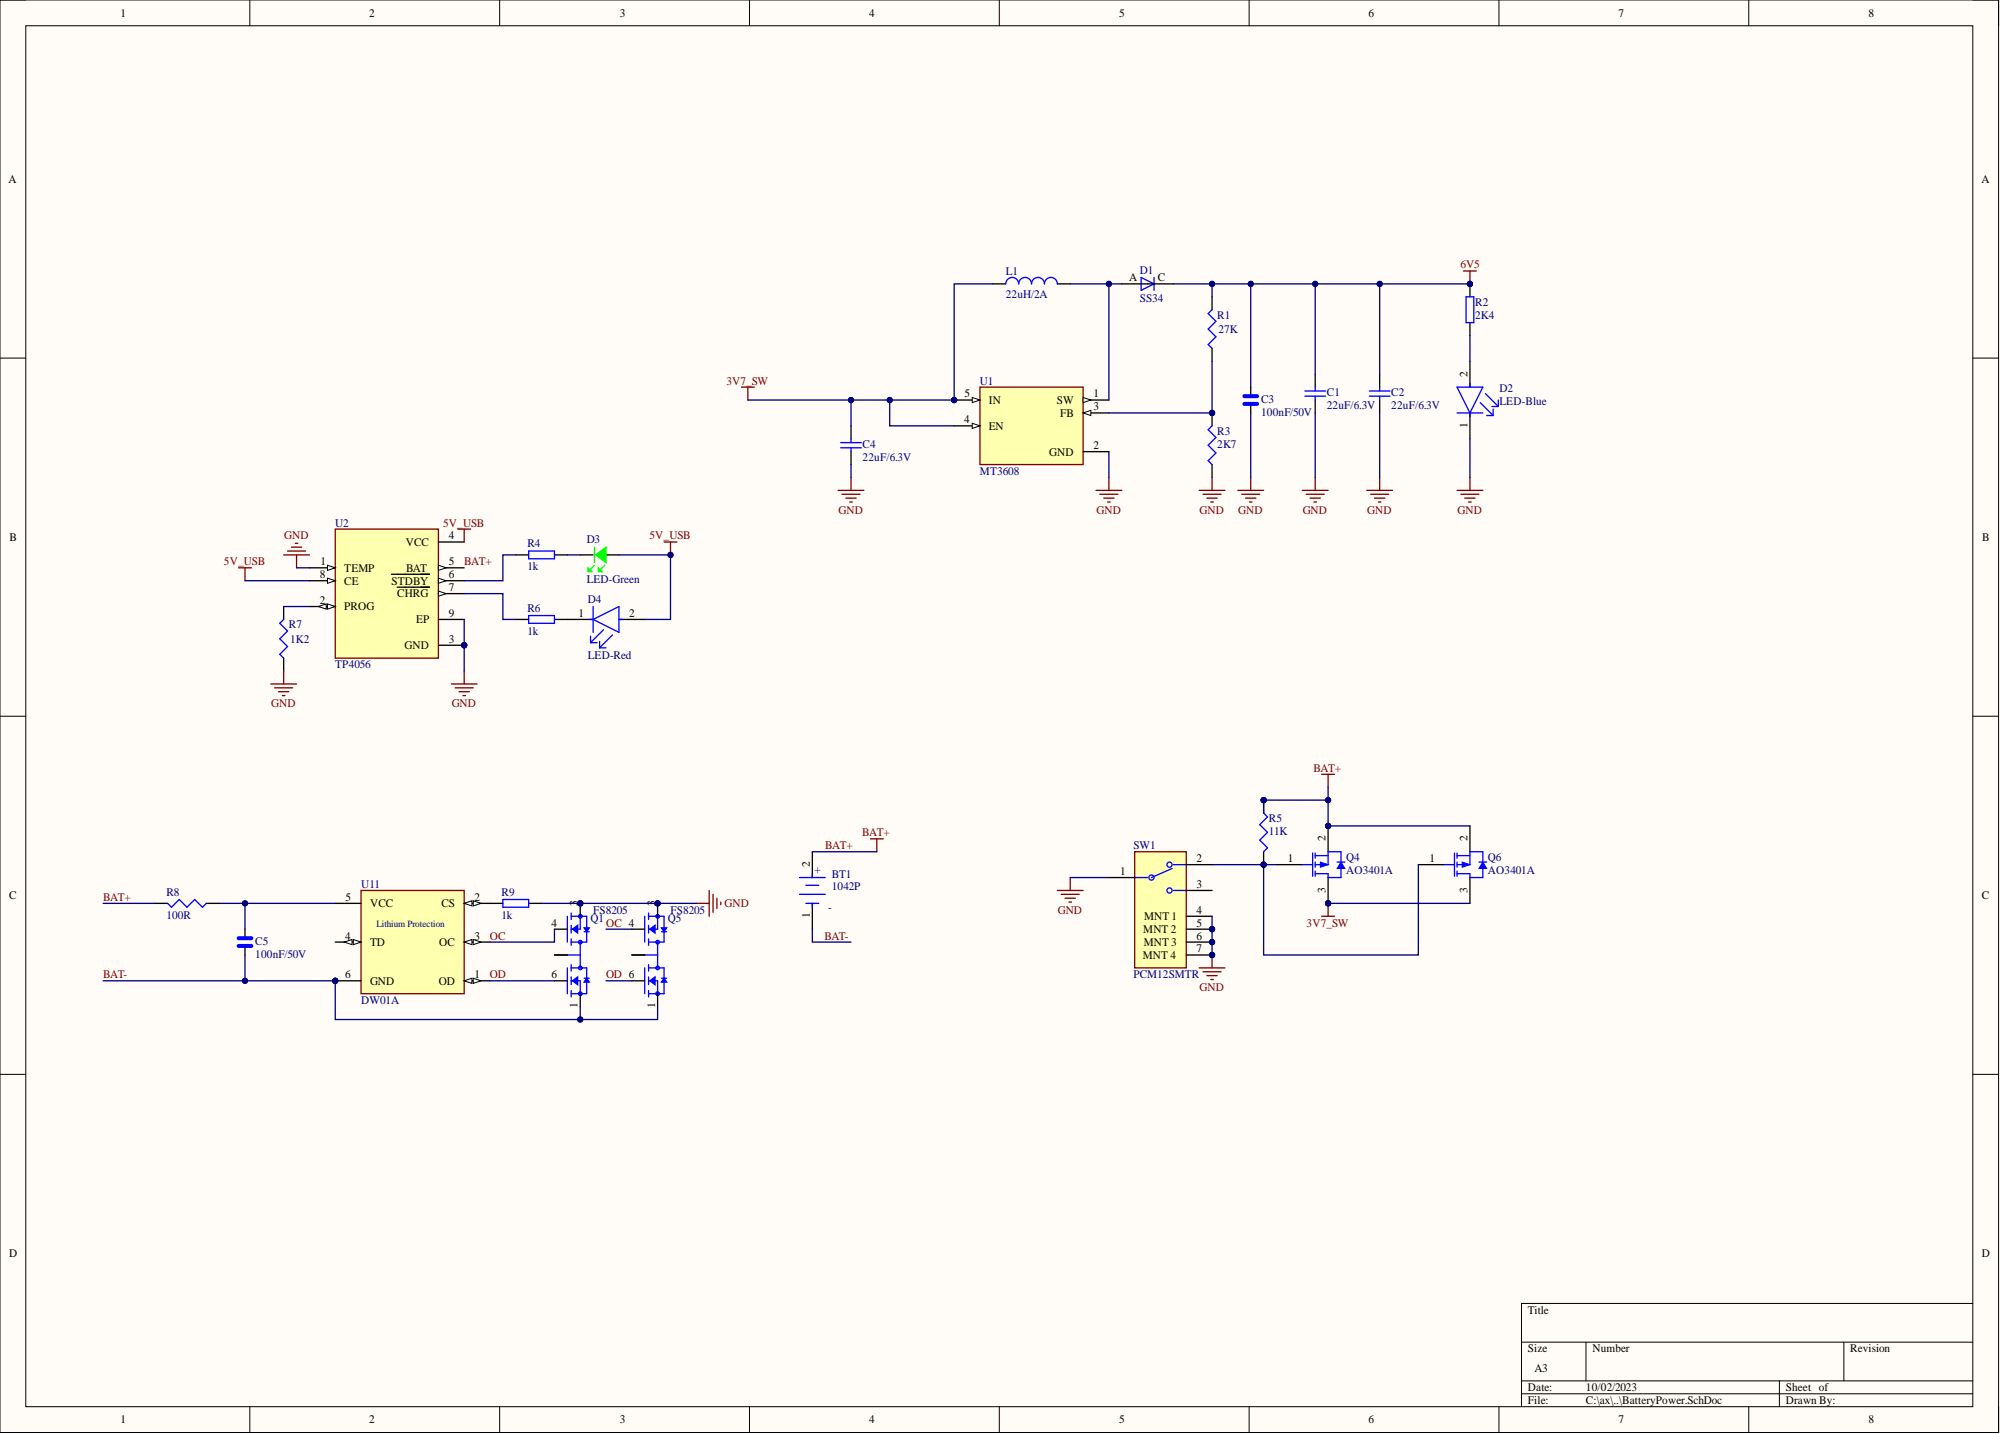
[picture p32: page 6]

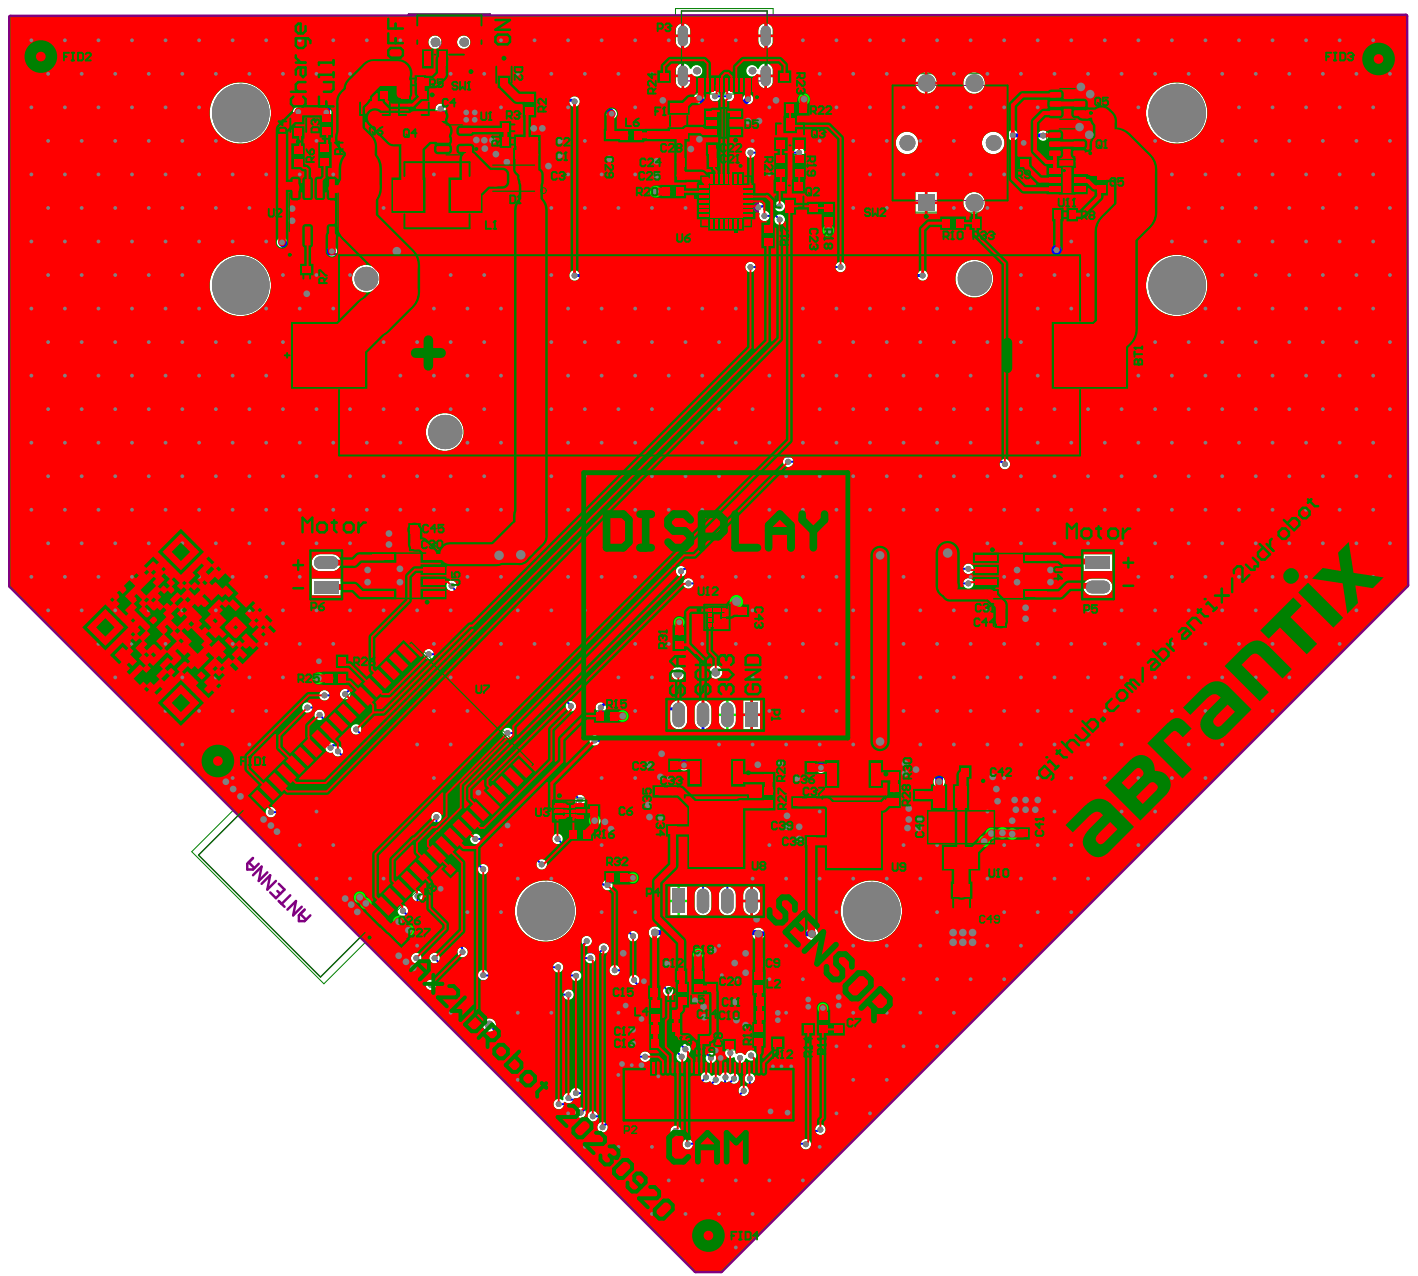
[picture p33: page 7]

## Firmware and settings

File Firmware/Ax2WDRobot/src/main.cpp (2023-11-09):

#include <Arduino.h>
#include <SPI.h>
#include <ArduinoOTA.h>
#include "CoreDefinitions.h"
#include "CameraHandler.h"
#include "MotorDriver.hpp"
#include "Ultrasonic.h"
#include "Bitmap.h"

//
// WARNING!!! PSRAM IC required for UXGA resolution and high JPEG quality
//            Ensure ESP32 Wrover Module or other board with PSRAM is selected
//            Partial images will be transmitted if image exceeds buffer size
//

AxWebServer axWebServer;
AxButton axButton;
Ultrasonic ultrasonic;
bool alwaysFalse = false;
unsigned long startupCompleteMillis;

//forward declarations
bool setFuses();
void configureOTA();
void processButtons();
void OnNetworkChanged();

void setup() {
  #ifdef SERIAL_TRACE
    Serial.begin(SERIAL_TRACE_BAUDRATE);
  #endif

  // Force the FLASH voltage regulator to 3.3v, disabling "MTDI" strapping check at startup
  bool fusesChanged = setFuses();

  if(fusesChanged)
  {
    TRACELN("Fuse setting changed");
  }

  Wire.begin(I2C_SDA_PIN, I2C_SCL_PIN);
  Wire.setClock(400000L);

  //Camera and Display use same I2C address so we will switch Clk line between those two devices/buses
  //LOW: Display
  //HIGH: Camera
  pinMode(TWI_SEL_PIN, OUTPUT);

  AxDisplayInstance.Init(&Wire);
  AxDisplayInstance.DisplayBitmap(epd_bitmap_picasso, 1024);
  delay(3000);
  AxDisplayInstance.Display("Examining\nHardware");

  MotorDriverInstance.Init();

  /* Hack to assure that VERSION_PROGMEM isn't optimized away from binary firmware file */
  if(alwaysFalse)
  {
    Serial.print(VERSION_PROGMEM);
  }

  Serial.setDebugOutput(true);
  Serial.println("Startup...");

  AxEEPROMInstance.Init();
  axButton.Init();
  ultrasonic.Init();
  axWebServer.Init();
  AxNetworkInstance.Setup(&(EEPROMData.IPConfiguration));
  AxNetworkInstance.ConnectionChanged = OnNetworkChanged;
  CameraHandlerInstance.Init();

  startupCompleteMillis = millis();
}

void loop() 
{
  axWebServer.Process();
  AxDisplayInstance.Process();
  axButton.Process();
  AxNetworkInstance.Process();
  ultrasonic.Process();
  processButtons();
  CameraHandlerInstance.Process();
  MotorDriverInstance.Process();
}


void OnNetworkChanged()
{
  TRACELN("Restarting Webserver");
  axWebServer.OnNetworkChanged();
}

void factoryReset()
{
    TRACELN("FACTORY RESET");
    //Perform factory reset but keep MAC address;
    AxDisplayInstance.Display("\n  FACTORY RESET\n");
    AxEEPROMInstance.LoadEEPROM(true);
    delay(3000);
    ESP.restart();
}

void processButtons()
{
  if(axButton.IsButtonJustPressed(BUTTON_TYPE_FRONT))
  {
    TRACELN("Disable Screen Saver");
    AxDisplayInstance.DisableScreenSaver();
    AxDisplayInstance.DisplayBitmap(epd_bitmap_monalisa, 1024);
    delay(3000);
  }

  /* Check if Front button was pressed for long time - either directly at startup or at a later time */
  if(axButton.IsButtonPressed(BUTTON_TYPE_FRONT))
  {
    if(5000 <= axButton.GetCurrentPressDuration(BUTTON_TYPE_FRONT))
    {
      TRACE("front button pressed for ");
      TRACE(millis() - startupCompleteMillis - axButton.GetCurrentPressDuration(BUTTON_TYPE_FRONT));
      TRACE(" ms since start ");
      TRACELN();
      if(3000 > millis() - startupCompleteMillis - axButton.GetCurrentPressDuration(BUTTON_TYPE_FRONT))
      {
        factoryReset();
      }
      else
      {
        //Perform soft reset;
        AxDisplayInstance.Display("\n     REBOOT\n");
        delay(3000);
        ESP.restart();
      }
    }
  }
}

// Force the FLASH voltage regulator to 3.3v, disabling "MTDI" strapping check at startup
//https://github.com/espressif/esp-idf/tree/release/v3.2/examples/storage/sd_card#note-about-gpio12
bool setFuses()
{
  bool changed = false;
  
  //burning SDIO_TIEH -> sets SDIO voltage regulator to pass-thru 3.3v from VDD
  if ((REG_READ(EFUSE_BLK0_RDATA4_REG) & EFUSE_RD_SDIO_TIEH) == 0) 
  {changed = true; esp_efuse_reset(); REG_WRITE(EFUSE_BLK0_WDATA4_REG, EFUSE_RD_SDIO_TIEH); esp_efuse_burn_new_values();} 

  //burning SDIO_REG -> enables SDIO voltage regulator (otherwise user must hardwire power to SDIO)
  if ((REG_READ(EFUSE_BLK0_RDATA4_REG) & EFUSE_RD_XPD_SDIO_REG) == 0) 
  {changed = true; esp_efuse_reset(); REG_WRITE(EFUSE_BLK0_WDATA4_REG, EFUSE_RD_XPD_SDIO_REG); esp_efuse_burn_new_values();} 

  //burning SDIO_FORCE -> enables SDIO_REG and SDIO_TIEH
  if ((REG_READ(EFUSE_BLK0_RDATA4_REG) & EFUSE_RD_SDIO_FORCE) == 0) 
  {changed = true; esp_efuse_reset(); REG_WRITE(EFUSE_BLK0_WDATA4_REG, EFUSE_RD_SDIO_FORCE); esp_efuse_burn_new_values();} 

  return changed;
}

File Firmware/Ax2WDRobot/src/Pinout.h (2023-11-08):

/*
  Pinout.h - Pin definitions for Abrantix PayTestHub devices Frontend processor
  (c) Abrantix AG
*/

#ifndef __PINOUT_H
#define __PINOUT_H

//peripheral I2C bus (display, crypto...)
#define I2C_SDA_PIN 26
#define I2C_SCL_PIN 27

#define MOTOR_R2_PIN 12
#define MOTOR_R1_PIN 13
#define MOTOR_L2_PIN 14
#define MOTOR_L1_PIN 15

#define HSPI_MISO   12
#define HSPI_MOSI   13
#define HSPI_SCLK   14

#define ULTRASONIC_TRIG_PIN 4
#define ULTRASONIC_ECHO_PIN 2

#define FRONT_BUTTON_PIN  33
#define TWI_SEL_PIN       32


#endif

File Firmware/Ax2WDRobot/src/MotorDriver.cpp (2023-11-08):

/* MotorDriver.cpp */

#include "MotorDriver.hpp"
#include "Trace.h"

MotorDriver MotorDriverInstance;

Motor::Motor()
{
}

Motor::~Motor()
{

}

void Motor::SetupPwm(uint8_t pin)
{
    ledcAttachPin(pin, pwmChannel);
    ledcSetup(pwmChannel, PWM_Frequency, PWM_Resolution);
}

void Motor::SetSpeed(uint8_t speed)
{
    this->speed = speed;
    UpdatePwm(false);
}

void Motor::UpdatePwm(bool MotorStateChanged)
{
    if(MotorStateChanged)
    {
        switch(state)
        {
            case MotorState_Forward:
                SetupPwm(pinA);
                ledcWrite(pwmChannel, speed);
                pinMode(pinB, OUTPUT);
                digitalWrite(pinB, 0);
            break;
            case MotorState_Backward:
                SetupPwm(pinB);
                ledcWrite(pwmChannel, speed);
                pinMode(pinA, OUTPUT);
                digitalWrite(pinA, 0);
            break;
            case MotorState_Stop:
                pinMode(pinA, OUTPUT);
                digitalWrite(pinA, 0);
                pinMode(pinB, OUTPUT);
                digitalWrite(pinB, 0);
            break;
            default:
            break;
        }
    }
    else
    {
        if(state != MotorState_Stop)
        {
            ledcWrite(pwmChannel, speed);
        }
    }
}

MotorDriver::MotorDriver()
{
    motorL.pwmChannel = PWM_L_Ch;
    motorR.pwmChannel = PWM_R_Ch;

    motorL.pinA = MOTOR_L1_PIN;
    motorL.pinB = MOTOR_L2_PIN;
    motorR.pinA = MOTOR_R1_PIN;
    motorR.pinB = MOTOR_R2_PIN;
}

MotorDriver::~MotorDriver()
{
}

void MotorDriver::Init()
{
    Stop();
    SetSpeed(SPEED_DEFAULT);
}

/// @brief Stop both Motors
void MotorDriver::Stop()
{
    motorR.state = MotorState_Stop;
    motorL.state = MotorState_Stop;
    motorL.SetSpeed(0);
    motorR.SetSpeed(0);
    motorR.UpdatePwm(true);
    motorL.UpdatePwm(true);
}

void MotorDriver::Process()
{
}

void MotorDriver::SetSpeed(uint8_t speed)
{
    motorR.SetSpeed(speed);
    motorL.SetSpeed(speed);
    motorR.UpdatePwm(false);
    motorL.UpdatePwm(false);
}

void MotorDriver::Forward()
{
    motorR.state = MotorState_Forward;
    motorL.state = MotorState_Forward;
    motorR.UpdatePwm(true);
    motorL.UpdatePwm(true);
}

void MotorDriver::Backward()
{
    motorR.state = MotorState_Backward;
    motorL.state = MotorState_Backward;
    motorR.UpdatePwm(true);
    motorL.UpdatePwm(true);
}

void MotorDriver::Left()
{
    motorR.state = MotorState_Forward;
    motorL.state = MotorState_Stop;
    motorR.UpdatePwm(true);
    motorL.UpdatePwm(true);
}

void MotorDriver::Right()
{
    motorR.state = MotorState_Stop;
    motorL.state = MotorState_Forward;
    motorR.UpdatePwm(true);
    motorL.UpdatePwm(true);
}

void MotorDriver::RotateClockwise()
{
    motorR.state = MotorState_Backward;
    motorL.state = MotorState_Forward;
    motorR.UpdatePwm(true);
    motorL.UpdatePwm(true);
}

void MotorDriver::RotateCounterClockwise()
{
    motorR.state = MotorState_Forward;
    motorL.state = MotorState_Backward;
    motorR.UpdatePwm(true);
    motorL.UpdatePwm(true);
}

void MotorDriver::JoyStickControl(float x, float y)
{

    float overallSpeed = sqrt(x*x + y*y);
    //80...255
    uint8_t pwmOverallSpeed = map(overallSpeed * 255, 0, 255, SPEED_MIN, SPEED_MAX);
    uint8_t pwmXSpeed = map(abs(x) * 255 * overallSpeed, 0, 255, SPEED_MIN, SPEED_MAX);
    uint8_t pwmYSpeed = map(abs(y) * 255 * overallSpeed, 0, 255, SPEED_MIN, SPEED_MAX);

    TRACEPRINTF("overall:%d x:%d y:%d\n", pwmOverallSpeed, pwmXSpeed, pwmYSpeed);

    //lookup quadrant
    if(y==0 && y==0)
    {
        Stop();
    }
    //0...90°
    else if(x<0 && y<0)
    {
        motorL.SetSpeed(pwmYSpeed);
        motorR.SetSpeed(pwmOverallSpeed);
        if(motorR.state != MotorState_Forward || motorL.state != MotorState_Forward)
        {
            motorR.state = MotorState_Forward;
            motorL.state = MotorState_Forward;
            motorR.UpdatePwm(true);
            motorL.UpdatePwm(true);
        }
    }
    //90...180
    else if(x>0 && y<0)
    {
        motorL.SetSpeed(pwmOverallSpeed);
        motorR.SetSpeed(pwmYSpeed);
        if(motorR.state != MotorState_Forward || motorL.state != MotorState_Forward)
        {
            motorR.state = MotorState_Forward;
            motorL.state = MotorState_Forward;
            motorR.UpdatePwm(true);
            motorL.UpdatePwm(true);
        }
    }
    //180...270
    else if(x>0 && y>0)
    {
        motorL.SetSpeed(pwmOverallSpeed);
        motorR.SetSpeed(pwmYSpeed);
        if(motorR.state != MotorState_Backward || motorL.state != MotorState_Backward)
        {
            motorR.state = MotorState_Backward;
            motorL.state = MotorState_Backward;
            motorR.UpdatePwm(true);
            motorL.UpdatePwm(true);
        }
    }
    //270..360
    else if(x<0 && y>0)
    {
        motorL.SetSpeed(pwmYSpeed);
        motorR.SetSpeed(pwmOverallSpeed);
        if(motorR.state != MotorState_Backward || motorL.state != MotorState_Backward)
        {
            motorR.state = MotorState_Backward;
            motorL.state = MotorState_Backward;
             motorR.UpdatePwm(true);
            motorL.UpdatePwm(true);
       }
    }
    else
    {
        //TODO transients...
    }
}

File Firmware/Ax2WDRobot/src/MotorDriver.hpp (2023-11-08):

/* MotorDriver.hpp */

#ifndef __MOTOR_H
#define __MOTOR_H

#pragma once

#include <Arduino.h>
#include "Pinout.h"

#define PWM_Resolution  8
#define PWM_Frequency   5000

#define PWM_L_Ch        2
#define PWM_R_Ch        3

#define SPEED_MIN         130
#define SPEED_DEFAULT     200
#define SPEED_MAX         255

enum MotorState
{
    MotorState_Stop,
    MotorState_Forward,
    MotorState_Backward,
};

class Motor
{ 
private:
    uint8_t speed;
    void SetupPwm(uint8_t pin);

public:
    MotorState state;
    uint8_t pinA;
    uint8_t pinB;
    uint8_t pwmChannel;

    Motor();
    ~Motor();
    void SetSpeed(uint8_t speed);
    void UpdatePwm(bool MotorStateChanged);
};

class MotorDriver
{
private:
    Motor motorR;
    Motor motorL;
    void UpdatePwm(bool MotorStateChanged);

public:
  MotorDriver();
  ~MotorDriver();
  void Init();
  void Process();
  void Stop();
  void SetSpeed(uint8_t speed);
  void Forward();
  void Backward();
  void Left();
  void Right();
  void RotateClockwise();
  void RotateCounterClockwise();
  void JoyStickControl(float x, float y);
};

extern MotorDriver MotorDriverInstance;

#endif
